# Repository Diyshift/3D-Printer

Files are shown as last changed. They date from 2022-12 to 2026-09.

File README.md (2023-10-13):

# 3D Printing Stuff
A collection of 3D printer tools, mods, and random printables. 

My projects are 100% fueled by coffee. If you enjoy the work I do and would like to buy me one, you can do so here. Thank you for your support! 



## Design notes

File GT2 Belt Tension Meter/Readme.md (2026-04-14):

# GT2 Belt Tension Meter (RC2)

  
  

### DETAILS:
This 3D printed tension meter is designed to measure belt deflection to determine belt tension for Gates 6 and 9mm GT2 belts. The goal is to eliminate the need for phone apps that use frequency to determine tension and to provide an easily quantifiable and repeatable number to use when tensioning belts on a 3D printer. The repeatability and accuracy of this meter will be partially dependent on the build quality but you can expect  approximately ± 1.0N (0.25lb) accuracy on a carefully built and calibrated meter. 

Tested on the following printers: Voron Trident, 2.4, V.0, Salad Fork, and Switchwire.  Note: for other non listed printers please ensure you have clear access to at least 150mm of belt. This meter will not work on printers with belts that run inside of the extrusion channels. 

**CAUTION:** The instructions and tension lookup tables contained herein are to be used with the the RC2 STL files included in this repository only. Any modifications, remixes, or substitutions of the core components have the potential to change the meter's characteristics and accuracy. Many iterations and months of testing were done with the current design (RC2) prior to its release to ensure an accurate and repeatable device. 

---------------------------------------------------------------------------------------------------
**Complete Assembled and Calibrated Meters Available Here:** [](https://www.etsy.com/listing/1508462271/belt-tension-meter-for-3d-printers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) **US** &nbsp;&nbsp;&nbsp;&nbsp; [](https://west3d.com/collections/vendors?q=PF%20Makes) **US** &nbsp;&nbsp;&nbsp;&nbsp; [](https://store.dremc.com.au/products/3d-printer-belt-tension-meter-by-pf-makes?variant=44804998955177) **AU**

---------------------------------------------------------------------------------------------------

### Ready to build your own? 

Below are instructions as well as everything you need to source hardware and get started. For video instructions please check out the excellent step-by-step build guide that LeeMerie3D put together on his Youtube channel here:

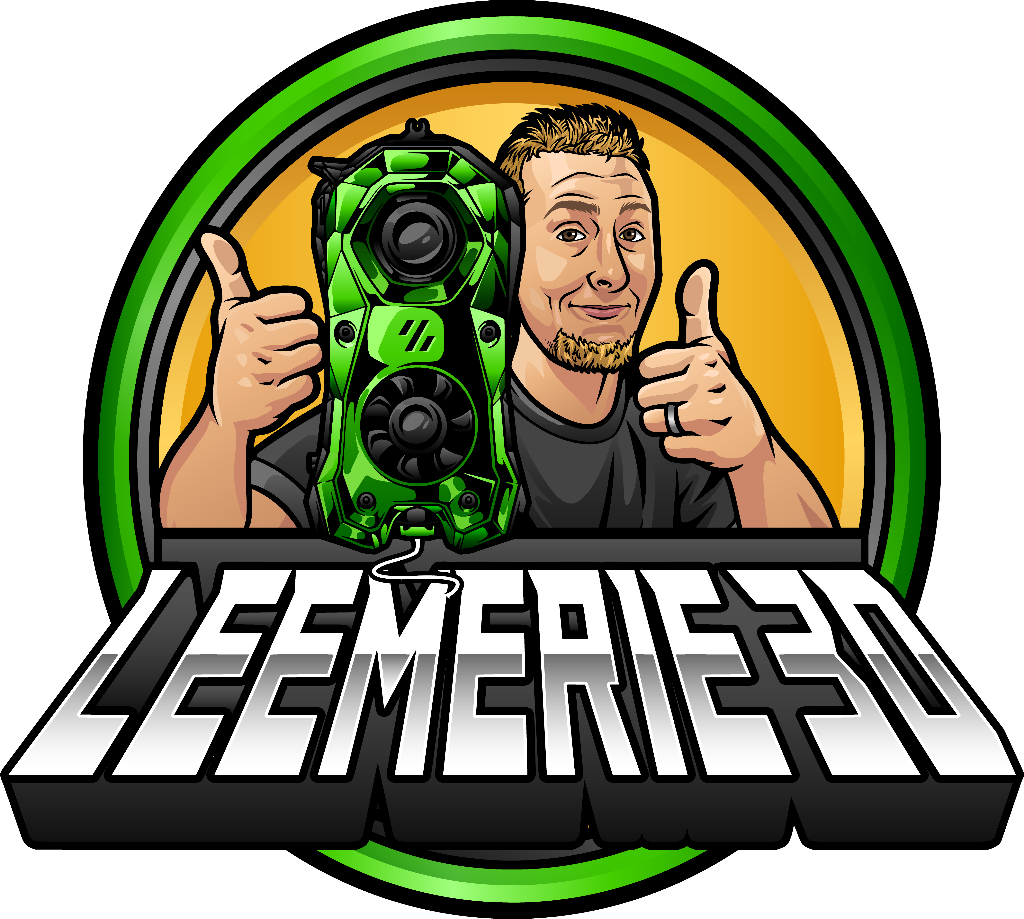
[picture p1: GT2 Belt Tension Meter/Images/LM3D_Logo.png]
[](https://www.youtube.com/watch?v=Ax2ZACkU6S8&t=1s)

### BOM:
Item | Qty
--- | ---
M3x7 Button Head Cap Screw (M3x6 BHCS also works) | 1
M3x25 Socket Head Cap Screw | 1
M3x8x0.6 Washer | 1
M2x10 Socket Head  Self Tapping Screws | 2
[0.81mm x 100mm (0.032” x 4”) Tempered steel music wire AKA "piano wire"](https://ksmetals.com/products/mw-032) | 1
[6mm OD x 0.6mm wire dia. x 50mm free length compression spring with 20 active coils (0.35N/mm spring rate)](https://www.amazon.com/dp/B076LTYY5K?psc=1&ref=ppx_yo2ov_dt_b_product_details) | 1
Complete Set of Printed [Parts](https://github.com/Diyshift/3D-Printer/tree/main/GT2%20Belt%20Tension%20Meter/STLs) | 1

**Complete Hardware Kits Available From The Following:** 

-----------------------------------------------------------------------------------------------------
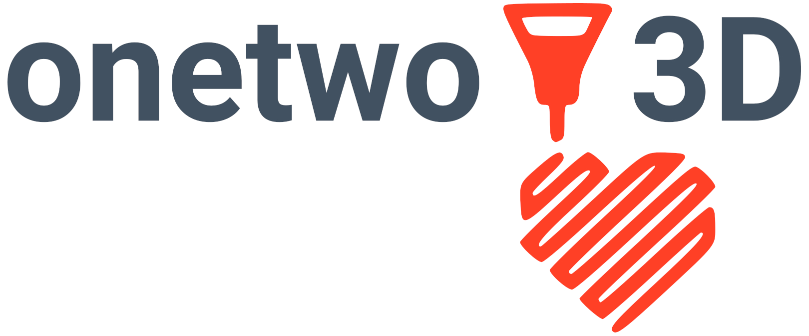
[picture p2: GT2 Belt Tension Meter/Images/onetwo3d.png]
[](https://www.etsy.com/listing/1508474957/hardware-kit-for-diy-3d-printer-belt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) **US** &nbsp;&nbsp;&nbsp;&nbsp; [](https://west3d.com/products/hardware-kit-for-diy-3d-printer-belt-tension-meter-by-pf-makes) **US** &nbsp;&nbsp;&nbsp;&nbsp; [](https://www.viperworx.uk/product/hardware-kit-belt-tension-meter-by-pf-makes) **UK** &nbsp;&nbsp;&nbsp;&nbsp;[](https://www.onetwo3d.co.uk/product/gt2-belt-tension-meter-hardware-kit) **UK**&nbsp;&nbsp;&nbsp;&nbsp;  [](https://store.dremc.com.au/products/3d-printer-belt-tension-meter-by-pf-makes?_pos=1&_sid=28fbfb08b&_ss=r) **AU** &nbsp;&nbsp;&nbsp;&nbsp; 

-----------------------------------------------------------------------------------------------------
[](https://www.3dptronics.com/voron-mods/gt2-belt-tension-meter-hardware-kit-by-pf-makes) **IT** &nbsp;&nbsp;&nbsp;&nbsp; [](https://www.replimat.eu/gt2-belt-tension-meter-hardware-kit/rt10204.2) **DE** &nbsp;&nbsp;&nbsp;&nbsp; [](https://www.3dlabtech.ca/product/belt-tension-meter/) **CA**

-----------------------------------------------------------------------------------------------------

### TOOLS:
 * M3 drill bit and holder 
 * ABS safe grease such as SuperLube Synthetic or Oatey/Harvey's silicone grease
 * 1.5, 2, and 2.5mm hex bit drivers. Ball end hex keys will likely give you a hard time here.
 * Toothpicks and Q-tips for applying grease
 * Hobby knife (X-Acto) 
 * Small flat needle file (optional)
 * Small triangular smooth cut file (for cleaning up gear teeth and tuning dovetail)
 * Cutter capable of cutting hardened music wire (do NOT use your nice flush cutters for this)

### PRINT SETTINGS:
 * Print in ABS or ASA for best results
 * Slide, needle and spring spacer components work best when printed on smooth or satin PEI
 * Layer height 0.2mm
 * 4 perimeters 5 top and 5 bottom layers
 * 40% grid infill
 * Single perimeter tops will improve the dialface text considerably
 * 0.4mm nozzle with 0.4mm line width throughout 
 * No seams allowed on needle or slide gear teeth, use blockers or adjust seam settings in your slicer. 
 * Color change at layer 18 for Base and layer 43 Pivot for dual color contrasting text.
 * Your printer should be well tuned for this project (for example, able to produce a near-perfect Voron cube). Any PA issues or over/under extrusion will likely result in a poorly performing meter.
   
### ASSEMBLY:

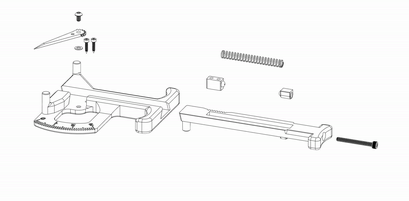
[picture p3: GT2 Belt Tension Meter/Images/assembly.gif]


1. Clean up printed parts as needed. Correct any zits, blobs or other print defects using a small file or hobby knife. Pay special attention to the gear teeth on the slide and needle. Carefully remove any stringing or blobs taking care not to change the tooth profile.
2. Check the fit between the slide and base. It should be loose enough to drop into the base freely without using force. The slide is designed to "float" in the base when in use. See gif below for proper fit. 
   
   

   If your slide it too tight you can adjust the fit in the base by shaving the dovetail in tiny increments with a triangular file on the angled face opposite the dial. 
4. Using a cotton swab, apply a light layer of grease to the spring channel  in the shaded area shown below. Do not lubricate the meter Base or Slide dovetail area as stiction may occur causing inaccurate readings.
5. Insert the spring, spacer, and spring as shown below.

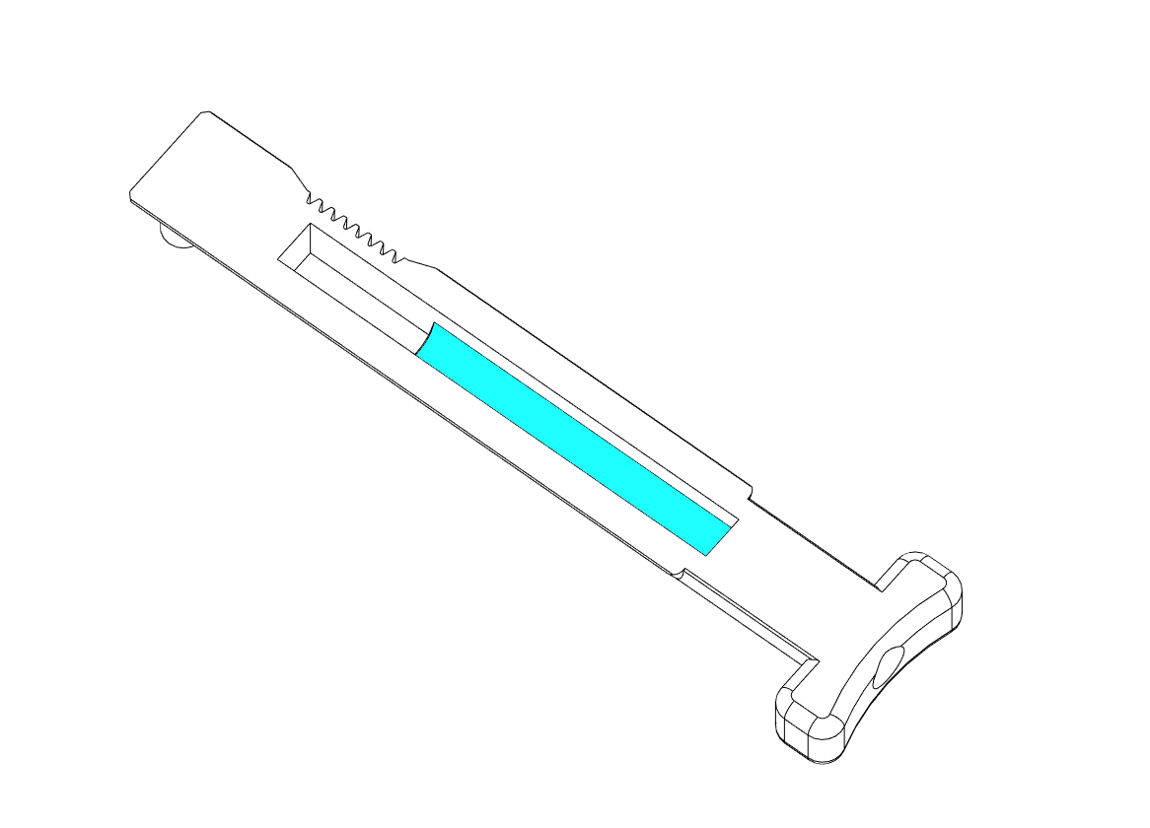
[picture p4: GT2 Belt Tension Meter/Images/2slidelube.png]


5. Insert the spring spacer, spring and spring block in that order as shown. Note of the position of the counterbores on the spring block, they should be facing down in this step.

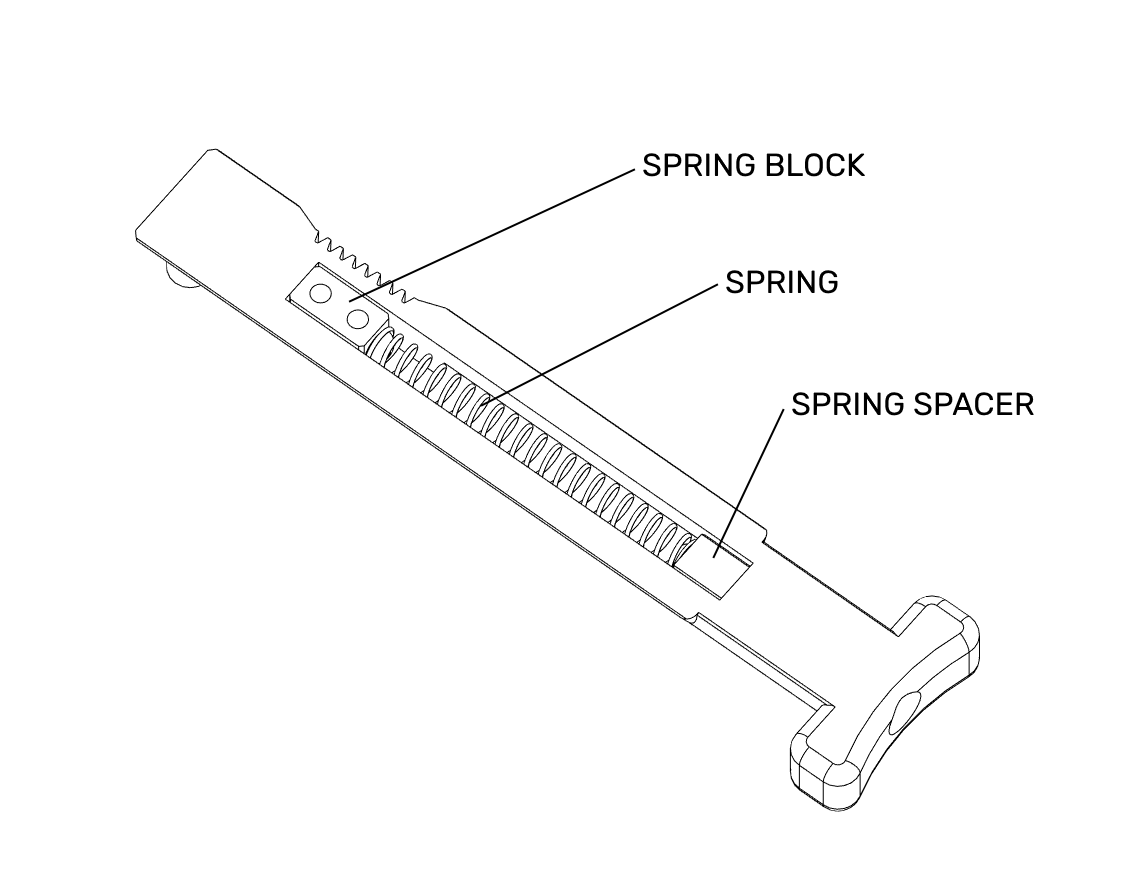
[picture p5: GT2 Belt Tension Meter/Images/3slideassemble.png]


 6. Flip the assembled slide and carefully insert the slide into the base as shown below. Spring tension should hold the parts in place.

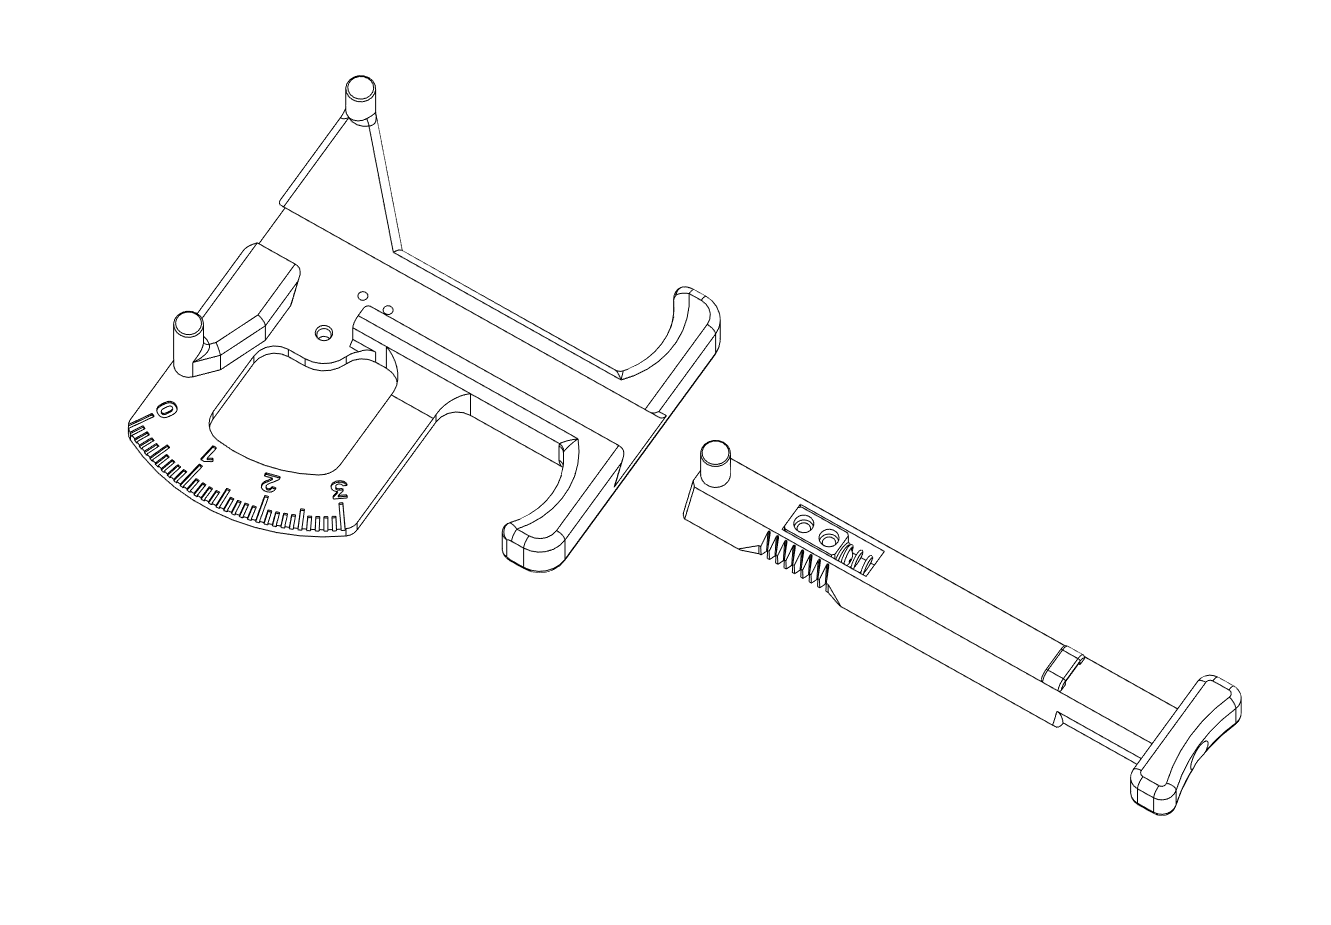
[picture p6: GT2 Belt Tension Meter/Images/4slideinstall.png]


 7. Align the slide with the front of the base so that they are flush and the two holes in the spring block are aligned with the corresponding holes in the base and secure the spring block to the base using two self-tapping M2 screws.

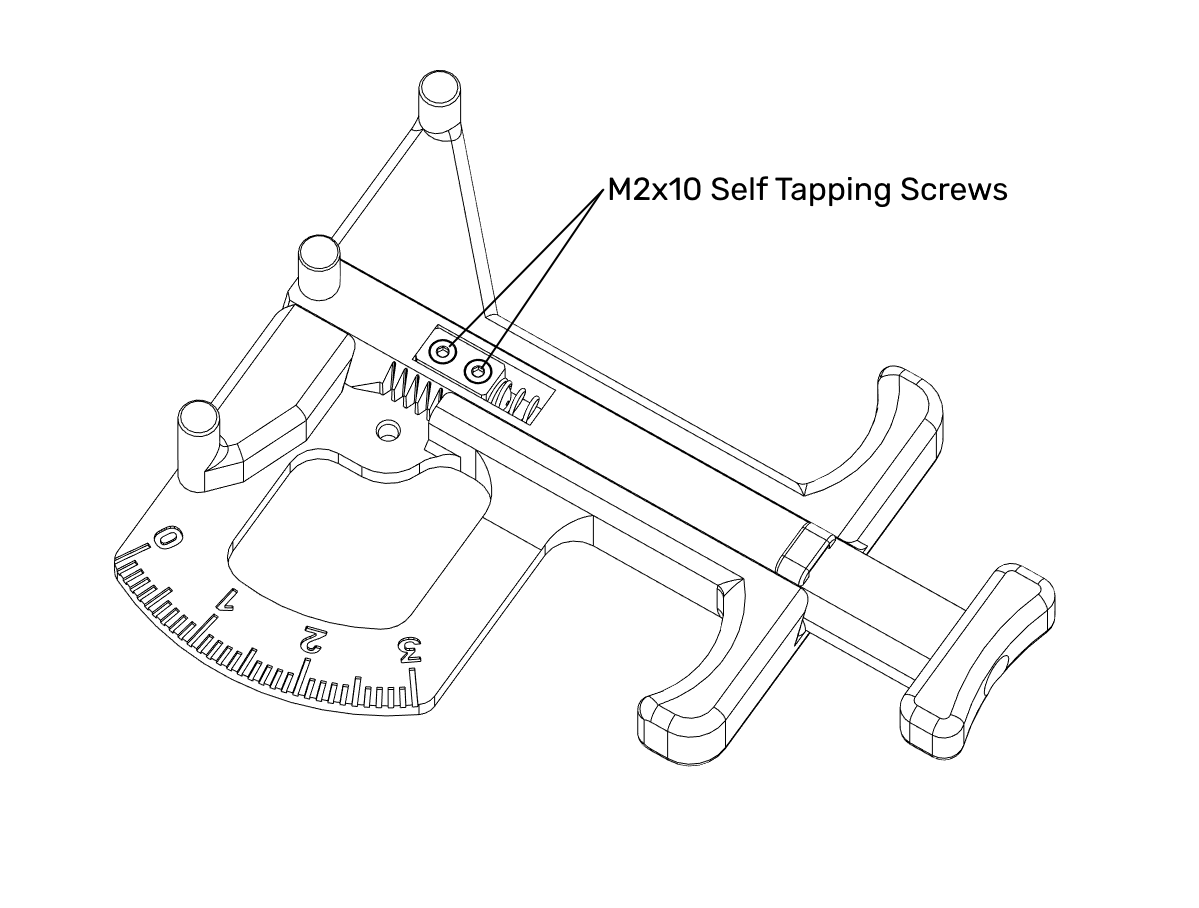
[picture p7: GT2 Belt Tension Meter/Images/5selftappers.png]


8. Depress slide plunger to check that the slide is moving smoothly and without binding.
9. Starting with a #2 needle use trial and error to determine the needle with the best fit. When aligned on the hole, the needle’s teeth will mesh with the slide’s teeth.

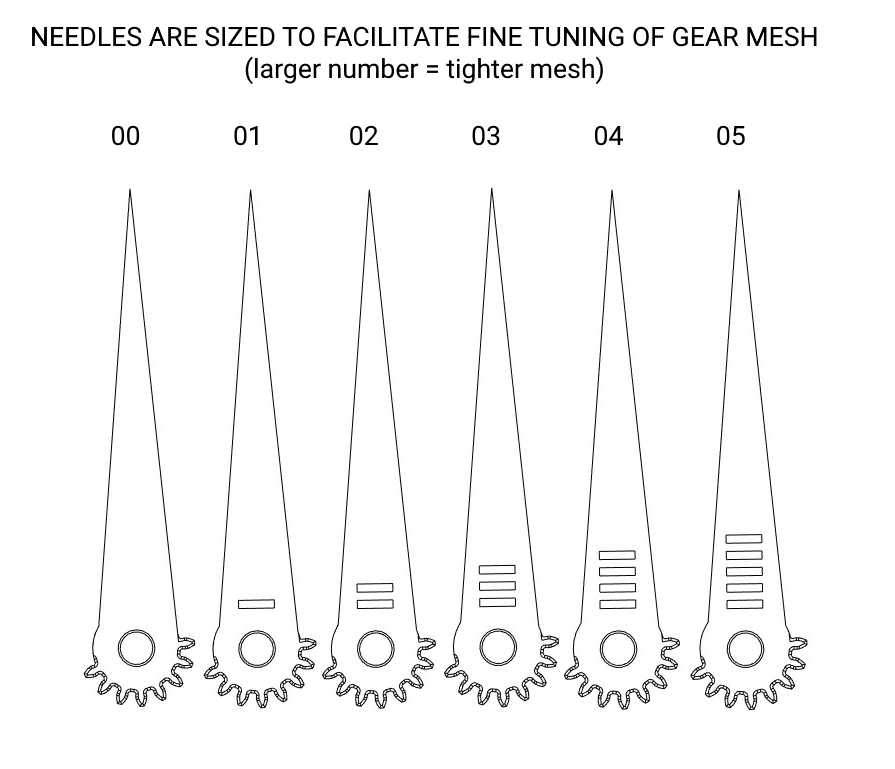
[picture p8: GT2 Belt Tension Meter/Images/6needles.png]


10. Ream the hole in the needle with a 3mm drill bit and check the fit using the M3x25 SHCS screw. The needle should rotate freely under its own weight. (tip: if you don’t own a 3mm drill bit you can use the M3x25 screw to ream the hole by screwing it into the needle and intentionally stripping the threads)
11. Insert the M3x6 BHCS through the top of the needle (as denoted by the circular stamp).
12. Place the M3x8 washer onto the base, aligning it with the hole with the smoothest side up. (some washers have a burr from stamping, this should face down for best result)
13. Secure the needle onto the washer with the M3x7 BHCS, making sure the needle aligns to the zero position and the round divot is facing up. 

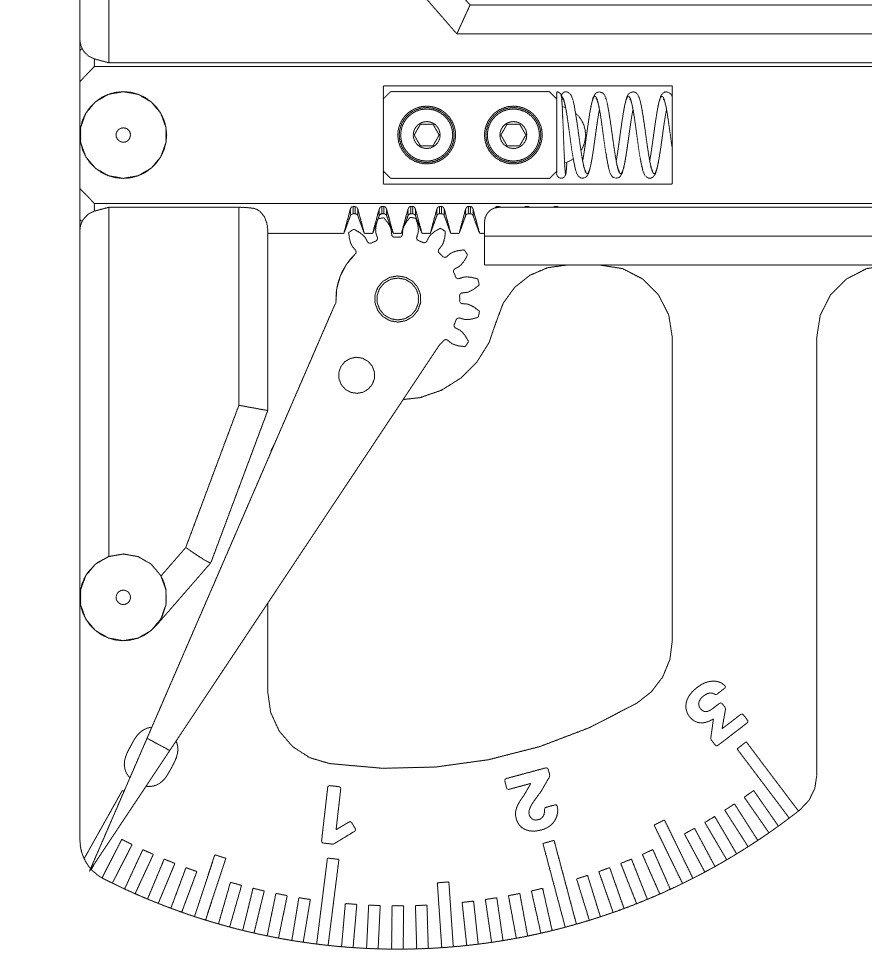
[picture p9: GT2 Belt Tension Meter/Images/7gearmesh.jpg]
 

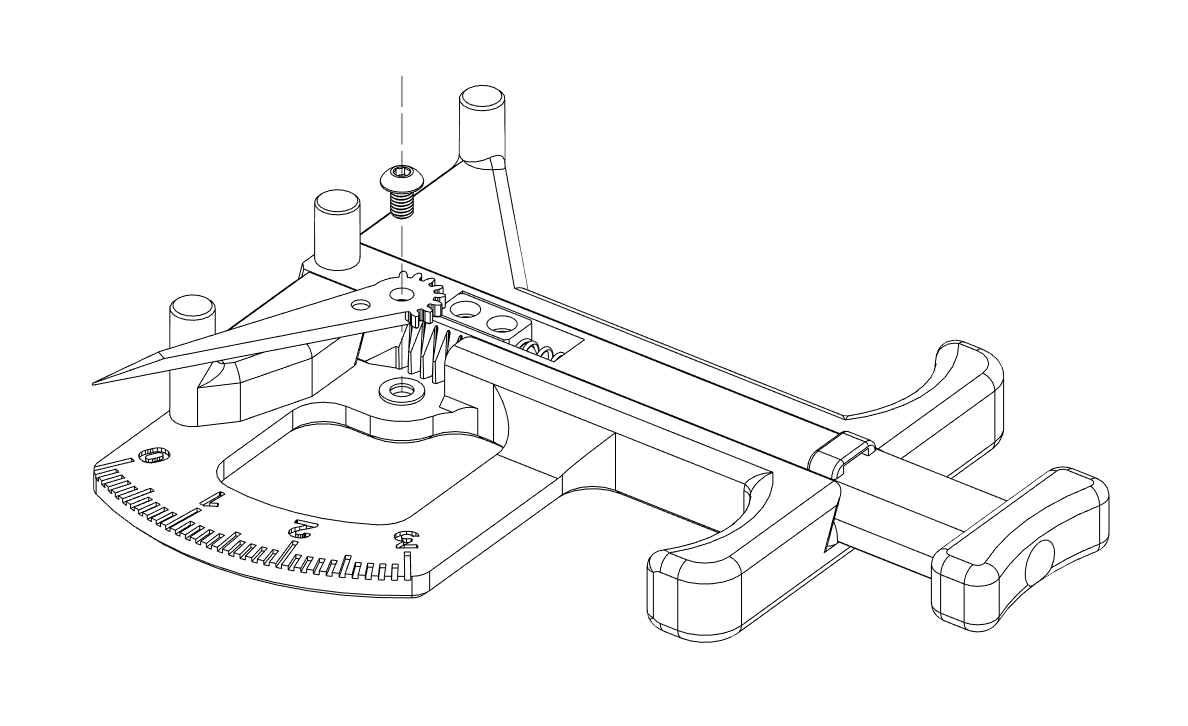
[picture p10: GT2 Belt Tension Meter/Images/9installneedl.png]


14. Tighten screw until just snug then back off in small increments until the needle moves freely.
15. Depress the slide’s plunger several times to ensure that the needle moves freely without jumping or binding.
16. Check the needle’s backlash by gently wiggling with a finger. If the needle moves more than ½ a tick on the dial, swap to the next size up and repeat this test. You want a needle size that gives you the least amount of backlash while still allowing smooth motion of the slide.
17. Once you have the correct needle selected, use a toothpick or similar to apply a very small amount of grease to the areas shown below.
18. Test to confirm that the needle spins freely on the screw.

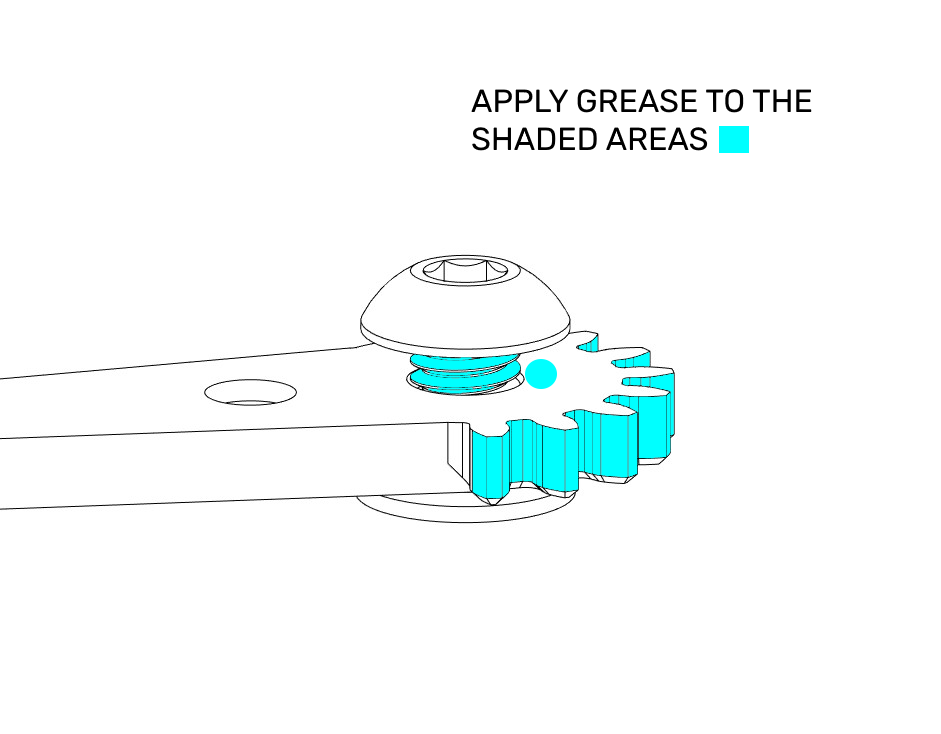
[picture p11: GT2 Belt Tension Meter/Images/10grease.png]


19. Flip the needle over and apply a very light layer of grease to the area that contacts the M3x8 washer, being careful not to get any on the lower threads.

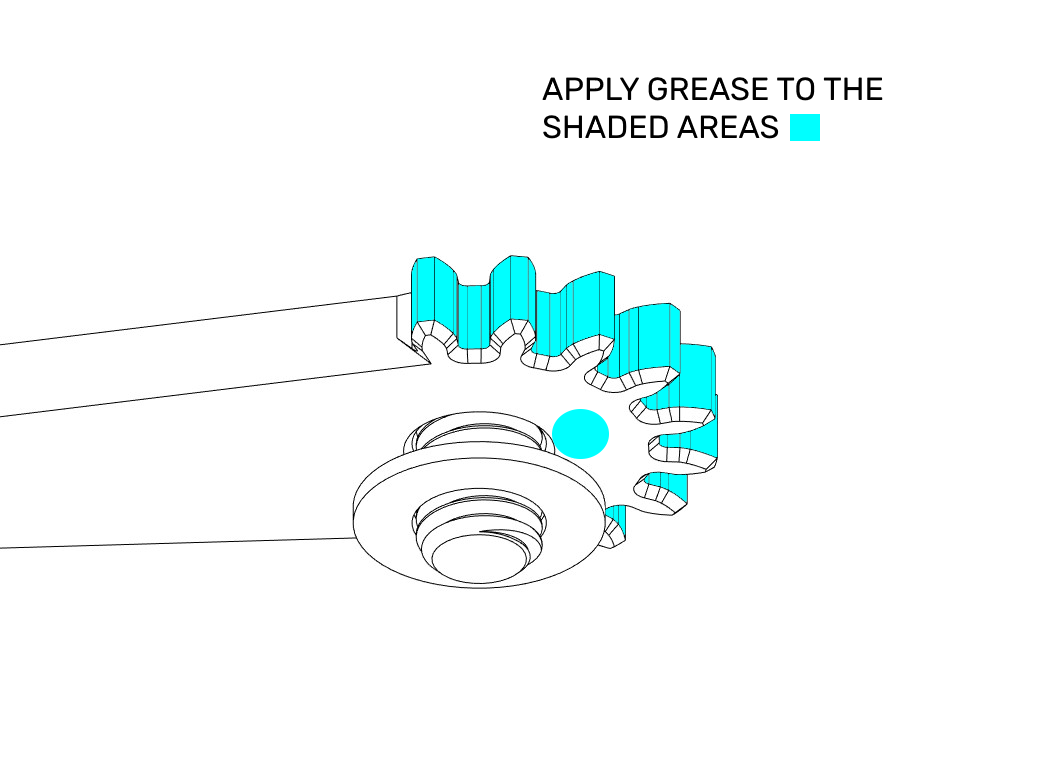
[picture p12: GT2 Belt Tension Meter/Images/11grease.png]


20. Apply a small amount of grease to the teeth on the needle as shown.
21. Place the M3x8 washer back onto the base.
22. Again, tighten the screw until just snug then back off until the needle swings freely.
23. Cycle the slide 20-30 times to make sure grease is distributed and the gears mesh.
24. Slowly cycle the slide several times and observe the needle’s motion. It should be smooth throughout its entire range with no sticking or jumping.  Adjust screw securing needle as needed to facilitate free movement.
25. Finally, install the M3x25 SHCS Preload Screw into the slide plunger as shown. This screw is threaded into plastic. Tighten until the head is flush with the plunger. Your meter is now assembled and ready for calibration.

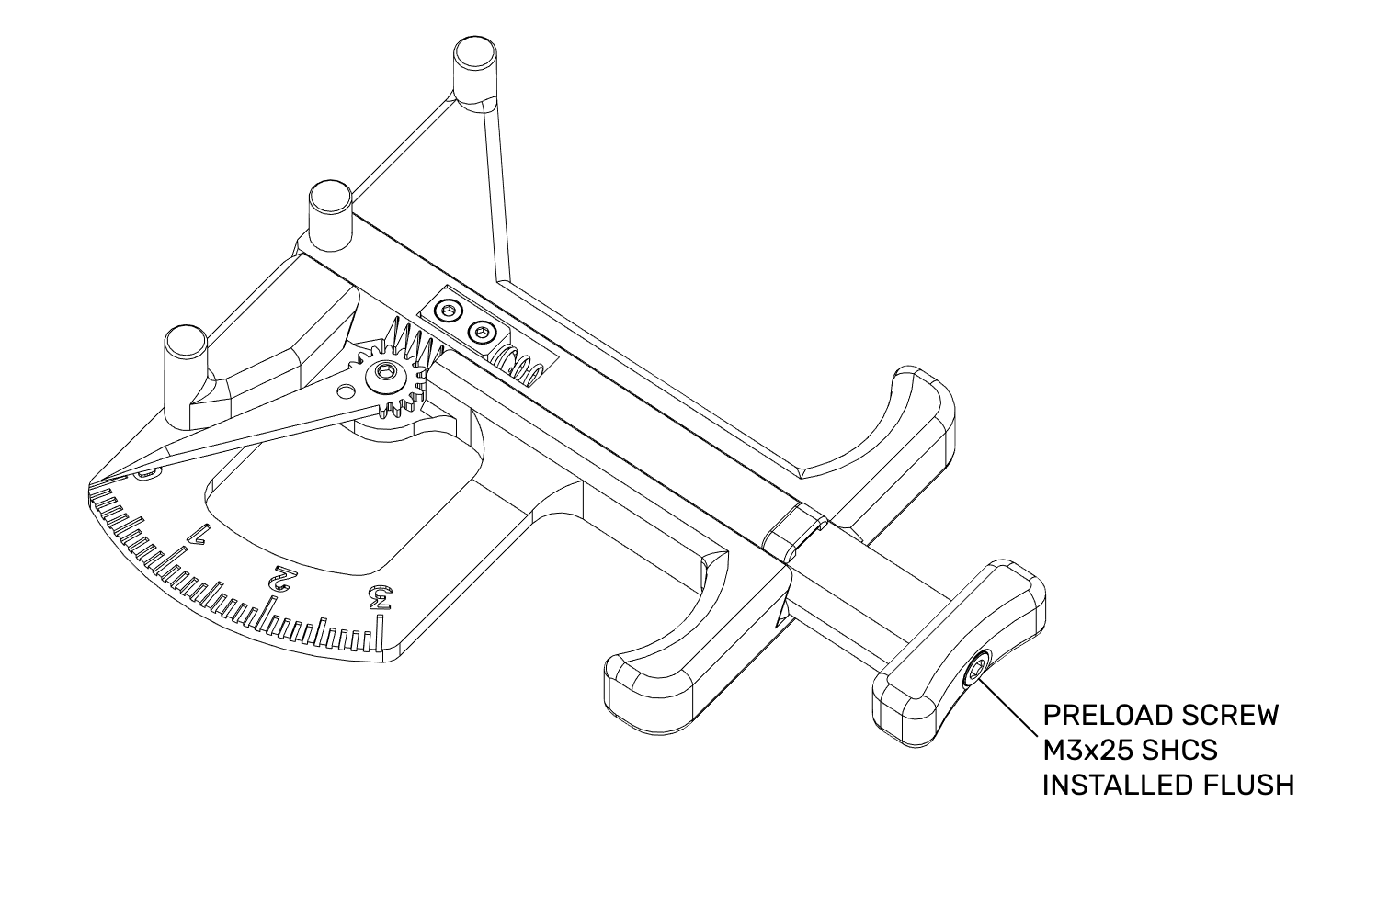
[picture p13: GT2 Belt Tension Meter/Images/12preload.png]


**Note:** If your meter dial is not resting on the zero mark you may need to loosen the two self tapping screws slightly in the spring block move needle to zero position then tighten screws back down. 

### CALIBRATION:

1. Cut music wire to 100mm and deburr the ends with a file.  (note: do not use your good side cutters for music wire, dremel cutoff or hard wire cutter recommended).
2. Glue the wire into the hole on the side of the calibration handle making sure it is fully seated and flush on the opposite side. Afterwards remove any burrs or glue from the hole in the calibration pivot. It should rotate freely on the left pin when installed.

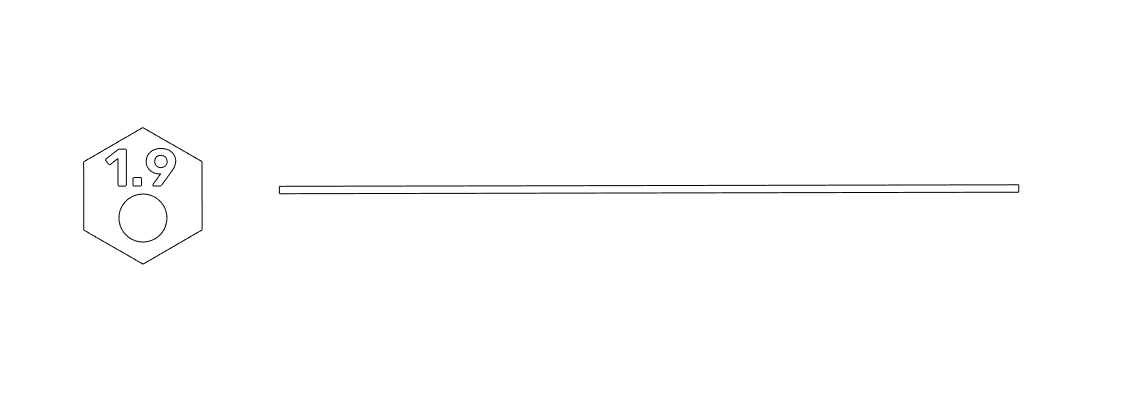
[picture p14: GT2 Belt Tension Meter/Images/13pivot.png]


3. Depress plunger and place calibration wire into the jaws making sure the pivot is seated all the way on the left pin as shown. Eye protection is recommended for this step.

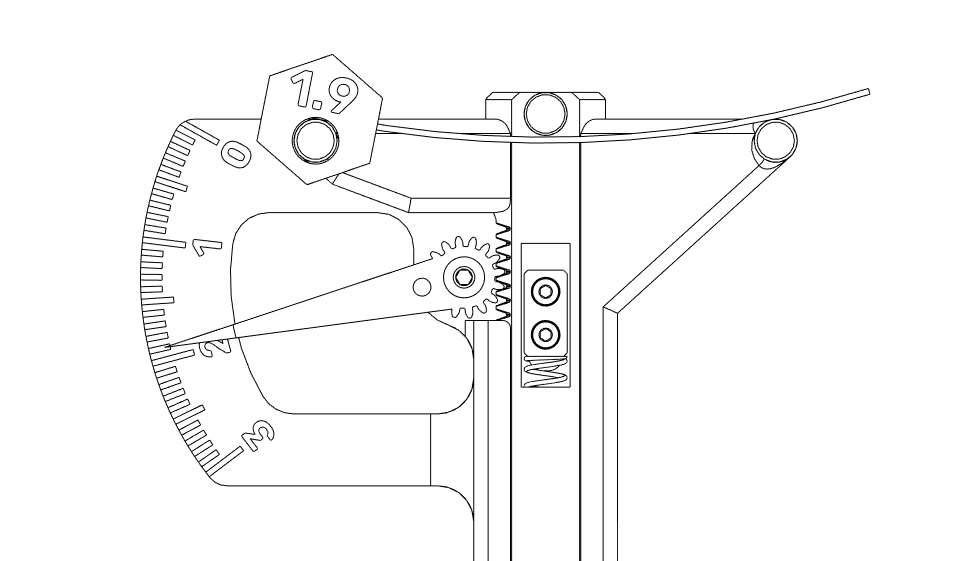
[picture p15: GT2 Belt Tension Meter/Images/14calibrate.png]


4. Slowly release the plunger and note the reading on the dial. Lightly tapping or “pumping” the plunger handle can help to settle the needle and get a better reading.
5. Tighten the preload screw one turn then depress and release the plunger again. Note that the reading has changed.
6. Repeat steps 3 - 5 until your meter consistently reads 1.9 when checking the deflection of the music wire.
7. Your meter is now calibrated and ready for use.

 ### ALTERNATIVE CALIBRATION:  
If straight tempered music wire is not available a suitable weight and spare section of belt can be used. A gallon plastic water jug and scale works well for this. Do not trust weights marked on fitness equipment, weigh them first. 

1. Suspend a 1.36Kg (3lb) weight vertically from a 250mm section of GT2 belt and measure the tension with the belt teeth in contact with the two outer pins on the meter as shown below in step 3.
2. Adjust the preload screw as needed until the meter reads consistently across several measurements.  2.1 for standard rubber or 2.2 EPDM high temperature belt.

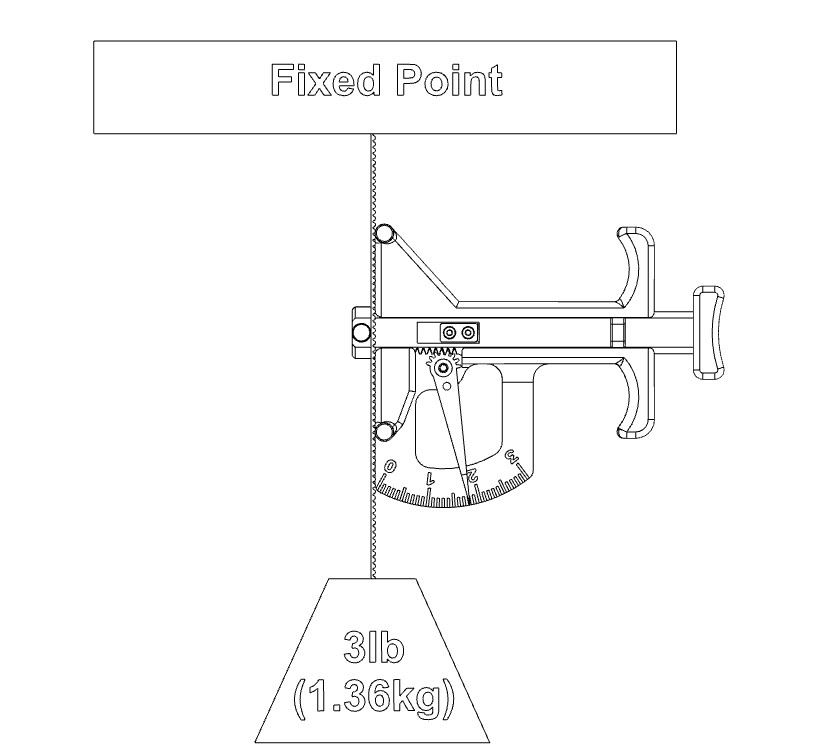
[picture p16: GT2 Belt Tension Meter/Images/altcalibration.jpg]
   

Calibration wire can be stowed on the center pin with wire secured beneath the slides wire keeper. 

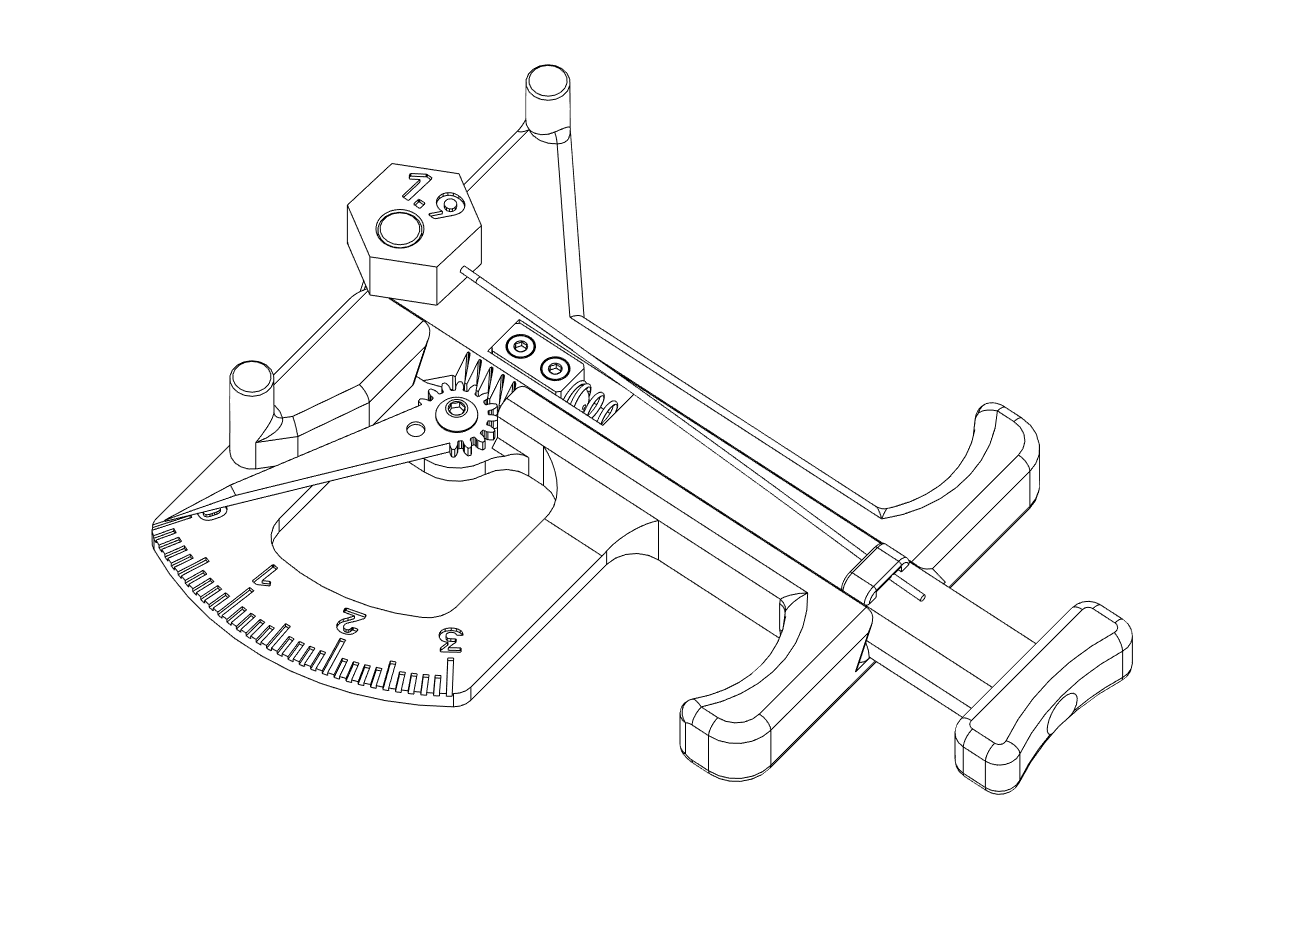
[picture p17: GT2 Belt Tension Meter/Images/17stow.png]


 ### TENSION MEASUREMENT A/B BELTS: 

 1. Printer should be cold for this test.
 2. Refer to your printer's documentation for proper belt tension or see table below.
 3. Center toolhead on X and then move Y until the X/Y idler centers are 150mm from the front idler centers. Motors should be on for this test. (note: unlike phone apps the 150mm distance is not a critical distance just a way to ensure that the toolhead is centered and to aid in obtaining repeatable results).
 4. Depress plunger and place meter on the 150mm belt span so that belt is routed through the gauge pins as shown.

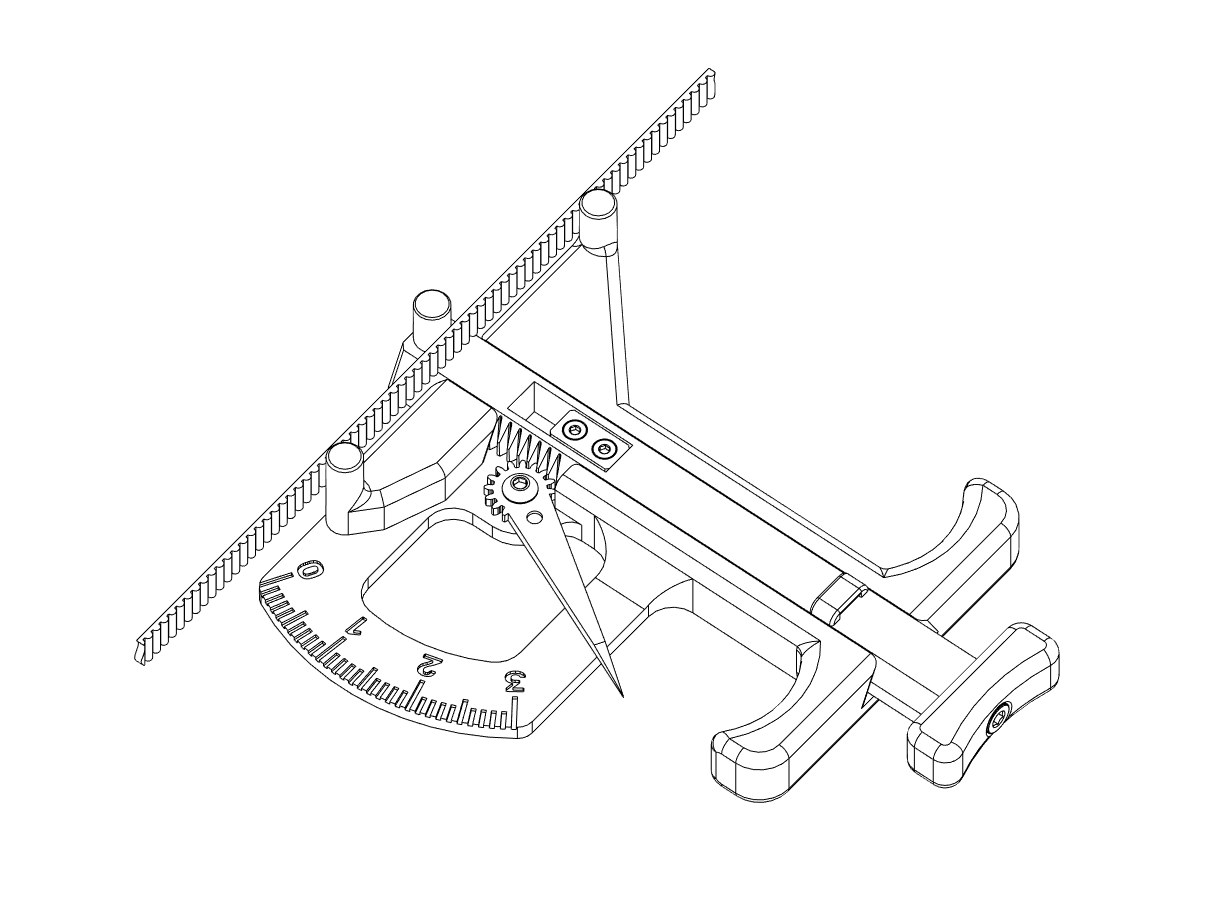
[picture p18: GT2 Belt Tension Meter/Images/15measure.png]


 5. Slowly release the plunger and note the reading on the dial. *rocking the meter very slightly fore and aft or lightly “pumping” plunger can help to settle the needle and get an accurate reading.
 6. Repeat three times to ensure you are getting consistent readings.
 7. Adjust belt tension then repeat steps 3-5 until you reach the desired tension (see table below) The A/B belt tensions can affect each other. Tightening one will also tighten the other. Go back and forth adjusting each until they are equal.

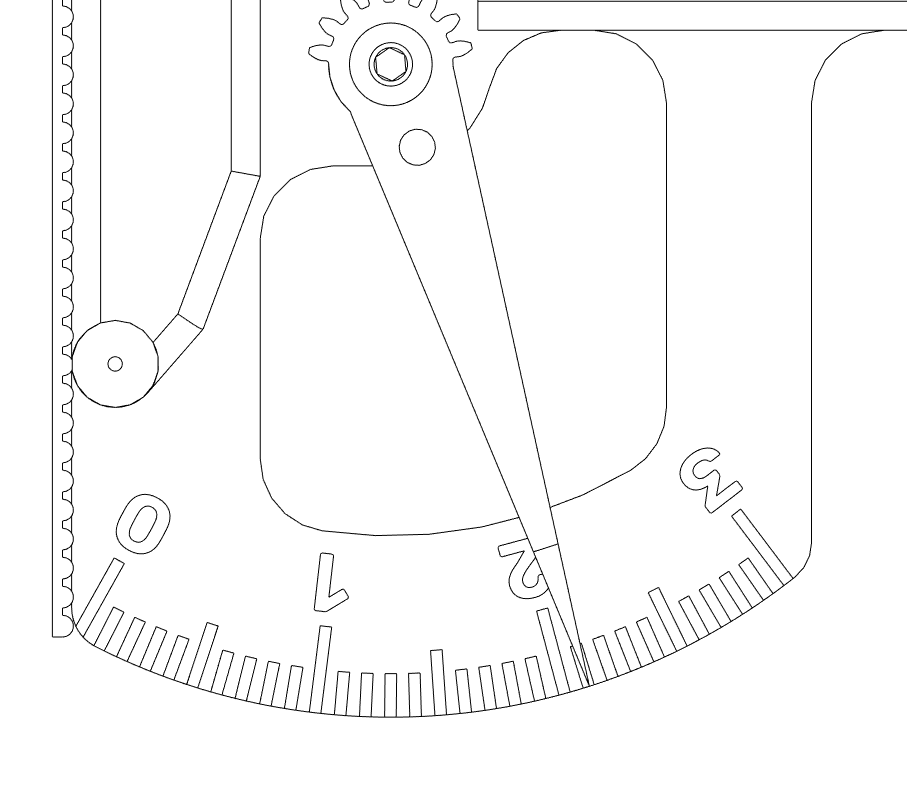
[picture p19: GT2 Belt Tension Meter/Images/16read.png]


8. Home X and Y to seat the belts then repeat steps 2-5 to verify that tension is correct and make followup adjustments as needed.
9. Your belts should now be properly tensioned. 

Note:  Depending on your style of printer your belt tension may increase slightly when utilizing a heated chamber so keep this in mind when selecting tensions in the higher range. Check your belts after a preheat to be sure you are not exceeding safe limits. When checking tension always remember to run the measured axis through its full range of travel before measuring to normalize the tension in the belt path. 

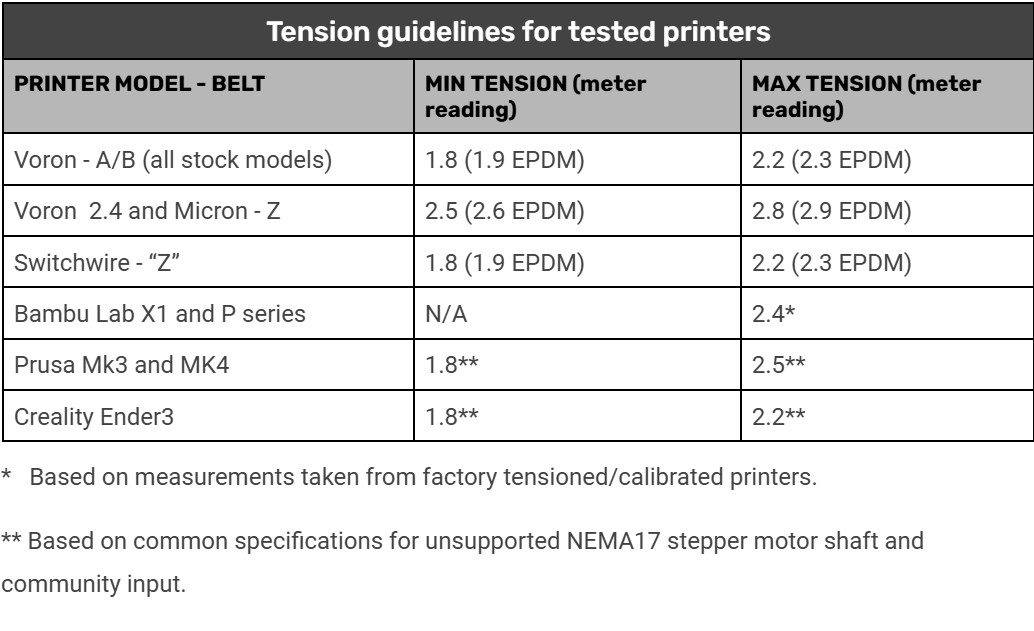
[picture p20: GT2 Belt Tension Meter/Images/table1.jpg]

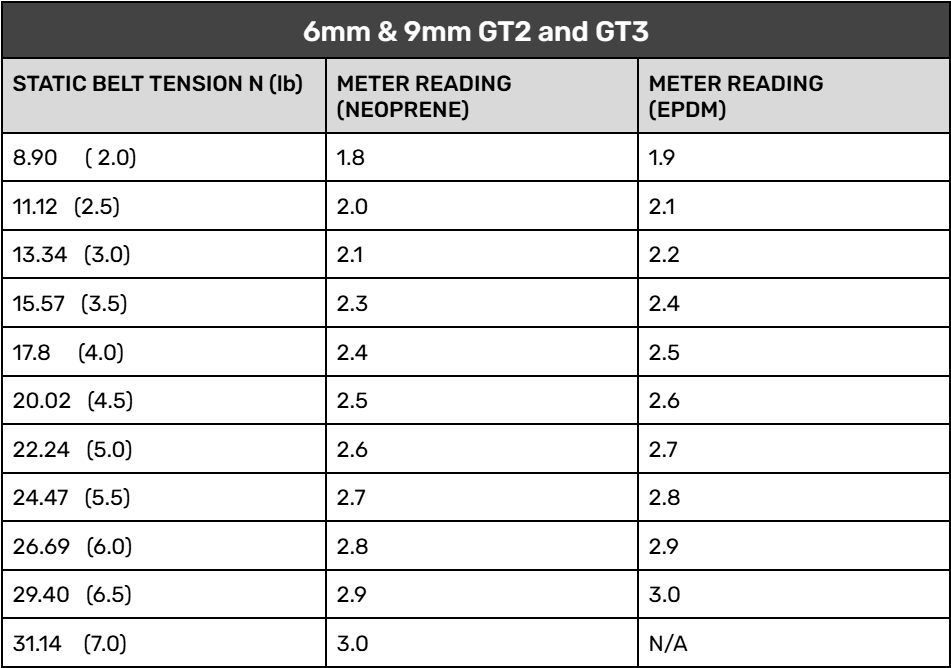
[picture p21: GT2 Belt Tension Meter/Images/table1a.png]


### Need a handy tension chart sticker?  Dr. Mursey has them here in his sticker shop: 

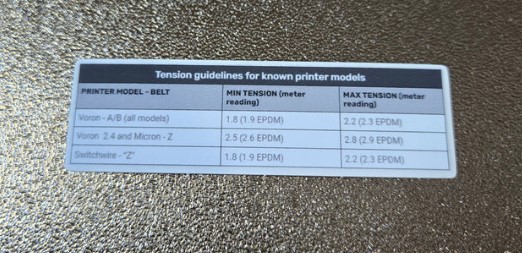
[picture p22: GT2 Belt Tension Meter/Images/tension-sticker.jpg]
[](https://drmursey.myshopify.com/products/pf-tensioner-chart)

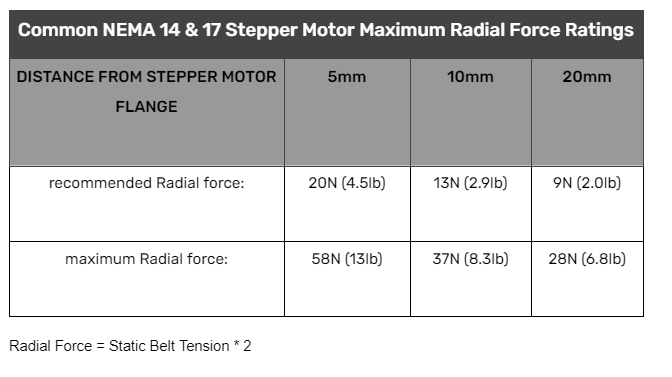
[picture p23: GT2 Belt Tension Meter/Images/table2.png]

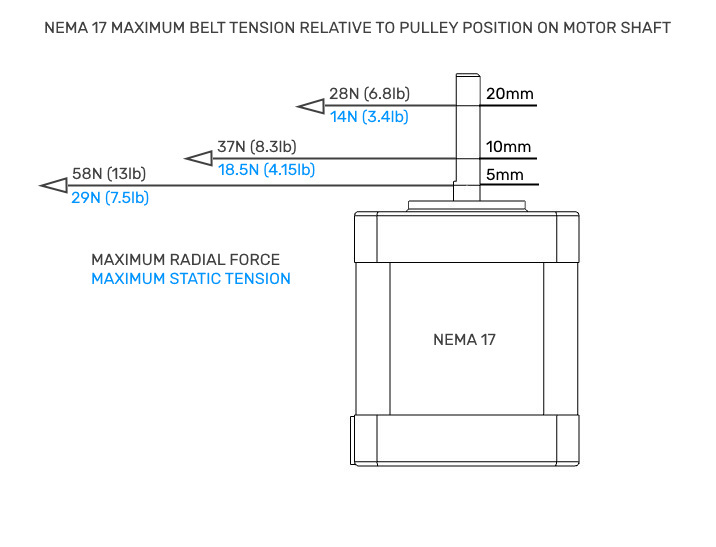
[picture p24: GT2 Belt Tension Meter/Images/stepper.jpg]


### CREDITS
Sincere thanks to the following for donating their time, plastic, and patience in helping to test and provide feedback on this design: 
 * Le0n2959
 * Moogoo (oogoom)
 * Yeri (yeriwyn)
 * Dokuu
 * Xivima
 * Mc-Red
 * Lillianamirrors
 * Pnewb



 My projects are 100% fueled by coffee. If you enjoy the work I do and would like to buy me one, you can do so here. Thank you for your support! 



This work is licensed under a
[Creative Commons Attribution-NonCommercial-ShareAlike 4.0 International License][cc-by-nc-sa].

[][cc-by-nc-sa]

[cc-by-nc-sa]: http://creativecommons.org/licenses/by-nc-sa/4.0/
[cc-by-nc-sa-image]: https://licensebuttons.net/l/by-nc-sa/4.0/88x31.png
[cc-by-nc-sa-shield]: https://img.shields.io/badge/License-CC%20BY--NC--SA%204.0-lightgrey.svg

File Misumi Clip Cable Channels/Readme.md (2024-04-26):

# Misumi Clip Cable Channels
 ### A collection of clips for 2020 extrusion to form channels to run/hide your wires 
 Now available for 1515 extrusions! See 1515 folder under STLs 
 


### Printing
  * Default voron settings
  * No supports needed

### Instructions:
 
Snap into extrusionslots to form wire channels. Cutouts models are provided for wire entry/exit. Shown here on vertical extrusions using the main channel clip for Trident:




Wire cutouts can also be used at at the top motor exits.  Thank you Voron Discord user cousin it VS.570 VT.1233 for this idea and image!


These are a modified version of Eddie's fantastic LED clips that can be found here: https://github.com/VoronDesign/VoronUsers/tree/master/printer_mods/eddie/LED_Bar_Clip

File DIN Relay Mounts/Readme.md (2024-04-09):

# DIN Relay Mounts 
 ### Mount single or dual channel relays on electonics bay DIN rails




### BOM

Size | Qty
--- | ---
Single or Double Channel Relay       | 1
Voron pcb_din_clip                       | 1
M2x6 Socket Head Self-Tapping Screws | 6

Relay screw hole spacing:  

Single Channel:  20mm x 45mm

Dual Channel:    33.25mm x 45mm

DIN Clip: https://github.com/VoronDesign/Voron-2/blob/Voron2.4/STLs/Electronics_Bay/pcb_din_clip_x3.stl

Dual Channel Relay: https://www.amazon.com/gp/product/B078478SZ9/ref=ppx_yo_dt_b_search_asin_title?ie=UTF8&psc=1

Single Channel Relay: https://www.amazon.com/gp/product/B00LW15A4W/ref=ppx_yo_dt_b_search_asin_title?ie=UTF8&psc=1

### Printing
  * Default voron settings
  * No supports needed

### Instructions:

  * Mount pcb_din_clip to the relay mount base using 2 M2x6 Socket Head Self-Tapping Screws
  * Install relay to mount using 4 M2x6 Socket Head Self-Tapping Screws

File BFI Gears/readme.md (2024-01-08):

# Trident Beefy Front Idler Gears (alpha version)
 ### Gears to keep your top and bottom tension adjustment screws in sync. For Clee's fantastic beefy front idlers found here: https://github.com/clee/VoronBFI



### BOM

Size | Qty
--- | ---
M3x8 BHCS    | 1
M3x6 BHCS (for recessed idler gear only) | 1

### Printing
  * Default voron settings
  * No supports needed

### Instructions:

  * Glue two larger gears to the heads of your M5x40 SHCS using superglue
  * Install BFI as you normally would and adjust top and bottom M5x40 SHCS so that belt runs centered 
  * Once centered install the smaller idler gear using an M3x8 BHCS screw (or M3X6 BHCS for recessed idler) do not overtighten. 
  * Gears should be a snug fit to eliminate backlash. Scale the center idler gear if needed to acheive a good fit.
  * If you would like or need more clearance print and install the recessed idler gear and use an M3x6 BHCS instead.

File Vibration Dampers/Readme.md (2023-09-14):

# Vibration Damping Coasters
 ### Uses sorbothane rings to dampen printer vibration 





### BOM

Size | Qty
--- | ---
Isolate It: Sorbothane Vibration Isolation Washer 70 Duro (0.5" ID - 1.5" OD - 0.5" Thick)* | 4
Self adhesive cork or similar anti skid (optional) | 4

*tested with Voron Trident 300, smaller lighter printers will likely require a lower durometer

### Printing
  * Default voron settings
  * No supports needed

### Instructions:
 
Add anti-skid cork or similar to bottom of cup and trim.  Place the sorbothane ring in the cup, then install the cap as shown and install underneath your stock printer feet.   



### My Trident input shaper results before and after adding the dampers: 



### Input shaper results with the ADXL mounted to my desk to measure its vibration: 



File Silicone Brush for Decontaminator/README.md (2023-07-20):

# Silicone Brush Mod for Decontaminator

A silicone brush mod for the Edwardyeeks decontaminator and brush mod that can be found [here](https://github.com/VoronDesign/VoronUsers/tree/master/orphaned_mods/printer_mods)

If you need this brush for your V0.2 check out MurseyThings remix [here](https://www.printables.com/model/522524-v02-nozzle-wiper-silicone-remix)

This design uses an inexpensive silicone bracelet that is cut into 18mm long segments to form the "bristles" of the brush using the supplied cutting guides. The cut silicone pieces are then placed into the slots in the brush holder and secured via a M3x50mm socket head caps screw. Sharpening the tip of the M3x50 SHCS to a point with a file is recommended but not necessary. If you choose not to sharpen the screw you can simply pierce the installed silicone flaps using the hole in the cut guide first with a tack or other shrarp object to make installing the unsharpened screw easier. 



### BOM

Size | Qty
--- | ---
M3x50 | 1
Heat-set Insert | 1
Silicone Wrist Band | 1 (2 if longer bristles are desired)

[CAD for alternative bristle guides](https://github.com/Diyshift/3D-Printer/tree/main/Silicone%20Brush%20for%20Decontaminator/CAD)

### Step 1.  Use the printed cutting guide to form the bristles. Print both guides and alternate 3 and 4 bristles segments in the brush holder.



### Step 2. Use a sharp object to pierce the the segment via the hole in the cutting guide. 



### Step 3. Ensure the band is fully inserted in the guide and make the final cut to length. 



### Step 4. Insert heat set insert followed my alternating 3 and 4 bristle segments. Make sure segments are fully seated and install the M3x50 Screw



### Step 5. Install your new silicone brush, check brush height and adjust as needed. 

The wrist bands I used for this can be found here: https://www.amazon.com/gp/product/B09263TPL9/ref=ppx_yo_dt_b_search_asin_title?ie=UTF8&psc=1  However any silicone band measuring approx 12mm wide and 2mm thick should work. If you have a soldering iron it is a good idea to test your bands first to ensure that they are in fact silicone and heat resistant enough to use for cleaning a heated nozzle. They should not melt when touched with the tip of the hot iron. 



Rainbow barf brush image courtesy of Discord user brad__r 

Thank you Le0n#2959 for the helping brainstorming the cutting guide! :)

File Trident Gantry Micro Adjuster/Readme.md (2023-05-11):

# A fidgety over complicated way to keep your extrusions in place while adjusting Trident rear gantry extrusion height

### BOM

Size | Qty
--- | ---
M3x10 | 3
M3x20 | 2
M3 Hammer Nuts | 3
M3 Nuts | 2



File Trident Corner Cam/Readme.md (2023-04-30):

# Trident Corner Pi Cam 
 ### 

View on 300 Trident with 150° lens

### BOM

Size | Qty
--- | ---
Arducam Arducam Lens Board OV5647    | 1
150° M12 Wide Angle Lens             | 1
1 Meter FFC Pi cam Cable             | 1
M3x5 BHCS                            | 3
M3x8 SHCS                            | 2
M3 Hammer Nuts                       | 1
M3 Heat Set Insert                   | 1
M2x6 Socket Head Self-Tapping Screws | 4

Pi Cam https://www.amazon.com/gp/product/B013JTY8WY/ref=ppx_yo_dt_b_search_asin_title?

150° Lens https://www.amazon.com/gp/product/B07FXF9Y1V/ref=ppx_yo_dt_b_search_asin_title?

Long FFC cable https://www.amazon.com/gp/product/B088CVNQHL/ref=ppx_yo_dt_b_search_asin_title?ie=UTF8&psc=1

### Printing
  * Default voron settings
  * No supports needed

### Instructions:

  * Mount Top Bracket to extrusions using M3x8 SHCS and hammer nuts. *this version is for left side mount only
  * Install Heatset in yoke then attach to Top Bracket using M3x6 BHCS. 
  * Insert FFC cable into the Pi cam module and secure. 
  * Pass FFC cable through rectangular slot in bottom of Cam Body. 
  * Insert Pi cam board into Cam body then install cover securing it with the M2x8 Socket head self tapping screws. 
  * Secure the completed camera module to the Yoke using 2 M3x6 BHCS threading them into the plastic of the Cam Body. Tighten only enough to hold the camera in      position, do not overtighten. 
  * Snap-in FFC cable channels are included to route your FFC cable down the vertical corner extrusion and into your electronics bay. There should be enough clearance to pass the FFC between the top deck panel and the frame. Use a 90° bend in the FFC cable and conseal with the exit port channels as shown. 
 




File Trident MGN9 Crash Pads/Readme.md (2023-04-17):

# Trident MGN9 Z Crash Pads

 ### Limit Z travel to minimize damage to X gantry and components in the event of a homing crash. Whoa means whoa!




### BOM

Size | Qty
--- | ---
Printed Crash Pad A.stl        | 3
Printed Crash Pad B.stl        | 3
M3x16 Socket Head Cap Screws   | 3
M3x5x4 Heat Set Inserts        | 3

### Printing
  * Default voron settings
  * No supports needed

### Instructions:

  * Install the tickest print bed/surface you plan to use. 
  * Home printer, Z-tilt
  * calibrate_z (only if using auto Z offset)
  * Center toolhead over bed and move to Z0 
  * Wipe any grease off of linear Z rail above the Z carriage and attach the crash pad as shown
  * Place 2-3mm hex key between the crash pad and the Z carriage to set the height
  * Tighten firmly and check to make sure it does not move
  * Now if z homing fails for any reason your z travel will be limited to Z-3. While this won't save your PEI it will stall the motors and prevent twisting your X extrusion and or breaking your X carriage components.

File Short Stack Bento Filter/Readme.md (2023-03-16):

# Short Stack Bento Box Carbon/HEPA Filter
 ### A shortened remixed version of the wonderful original design found here: https://www.printables.com/model/272525-bambu-lab-x1c-bentobox-air-filter



### BOM

Size | Qty
--- | ---
40x10 Axial Fan | 2
M3x8 Socket Head Cap Screws | 10
M3 Heat Set Inserts | 12
M3 Hammer Nuts | 2
40x80x15mm Hepa Filter | 1
6x3mm N52 Disc Magnets | 32
Acid-Free Activated Carbon

### Printing
  * Default voron settings
  * No supports needed

### Instructions:
In addition to shortening the modules, this remix relocates the wiring channels for cleaner wiring when used on Voron printers as well as mounting holes to secure it to the rear 2020 extrusion. For Trident mount the duct to 2020 rear extrusion using the two rearmost through holes, M3x8 screws and hammer nuts. Then secure fan mount and stack the remaining modules. 



This version for use with this size HEPA filter only: https://www.amazon.com/gp/product/B0782T7L6P/ref=ppx_yo_dt_b_search_asin_title?ie=UTF8&psc=1

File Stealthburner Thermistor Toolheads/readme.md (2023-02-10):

# Stealthburner Heatsink Thermistor Mod for Dragon Hotends
 ### Allows you to monitor the temperature of your heatsink where it mounts to the toolhead. Klipper can be configured to shutdown if this gets too hot in the event of a hotend fan failure.   



### BOM
100K Ohm NTC 3950 glass bead thermistor. (bead should measure approximately 1.6mm diameter x 3.3mm in length)

Here are the ones I use in my printersfor this mod. 
https://www.amazon.com/gp/product/B098TF372P/ref=ppx_yo_dt_b_search_asin_title?ie=UTF8&psc=1

### Printing
  * Default voron settings
  * No supports needed
  * Only the included rear portion of Stealthburner toolhead is needed to inplement this mod

### Instructions:
 Add a small dab of thermal grease to the thermistor before assembly. 
 
After connecting the thermistor to your control board add the thermistor entry to your printer.cfg file. I recommend setting at a lower shutdown temp to test before setting your final max_temp value
 
printer.cfg example: 

[temperature_sensor heatsink_temp]

sensor_type: Generic 3950

sensor_pin:      #port that thermistor is plugged into

min_temp: 0

max_temp: 50     #halt printer if ABS deflection temp is exceeded set to 90 after sucessful shutdown test at 50

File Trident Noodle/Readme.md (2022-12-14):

# Trident Reverse Bowden Noodle
Reverse bowden tube guide to keep it from rubbing the top panel.  Inspired by Logan#2225's clip on version.
 


### Printing
  * Default voron settings
  * No supports needed

### Instructions:
 
Slide onto reverse bowden tube prior to inserting into extruder coupling.

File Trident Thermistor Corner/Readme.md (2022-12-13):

# Trident Frame Thermistor Corner
 ### Mr. Thermistorfoot lets lets you cleanly run your thermistor from your electronics bay up through the center of your vertical extrusions for frame temp monitoring and thermal expansion compensation.  



### Printing
  * Default voron settings
  * No supports needed

### Instructions:
 
This is the A corner, so this will place your thermistor in the left-rear or front-right corner.

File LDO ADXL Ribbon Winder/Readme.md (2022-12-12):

# LDO ADXL Ribbon Winder
 ### Stores FFC ribbon cable for LDO Input Shaper Toolkit. 



### Printing
  * Default voron settings
  * No supports needed

### Instructions:
 
Snap halves together then line up the slot with the arrow on the lid. Insert the end of the ribbon cable and push until it stops. Use the large hole in the lid to wind up with your finger until just the blue tab is showing. Grasp knurled case and pull the ribbon when you need to remove it. 

You can view it in action here: https://youtube.com/shorts/ohC4sa6RvPU?feature=share



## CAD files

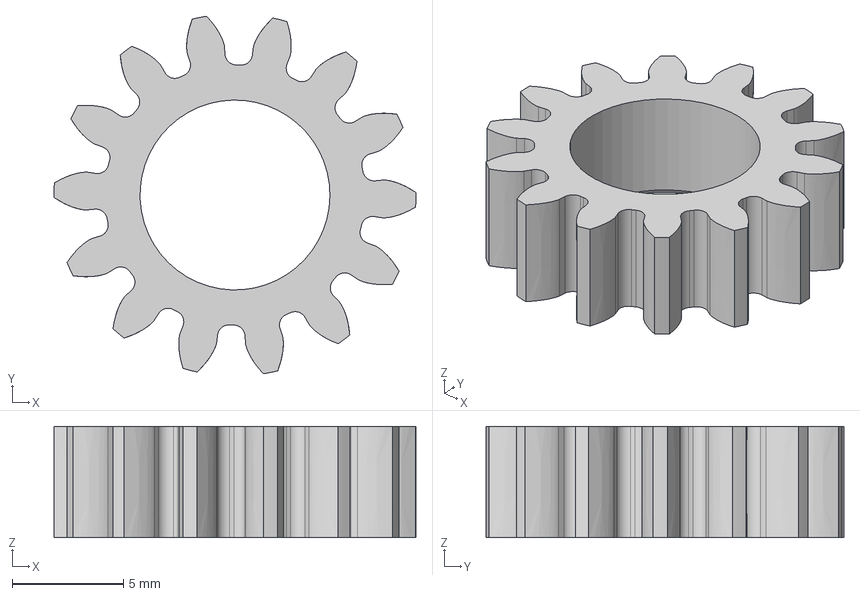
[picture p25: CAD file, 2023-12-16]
BFI Gears/CAD/BFI Main Gear 14 tooth 4X.step
16.3 x 16.1 x 5.00 mm

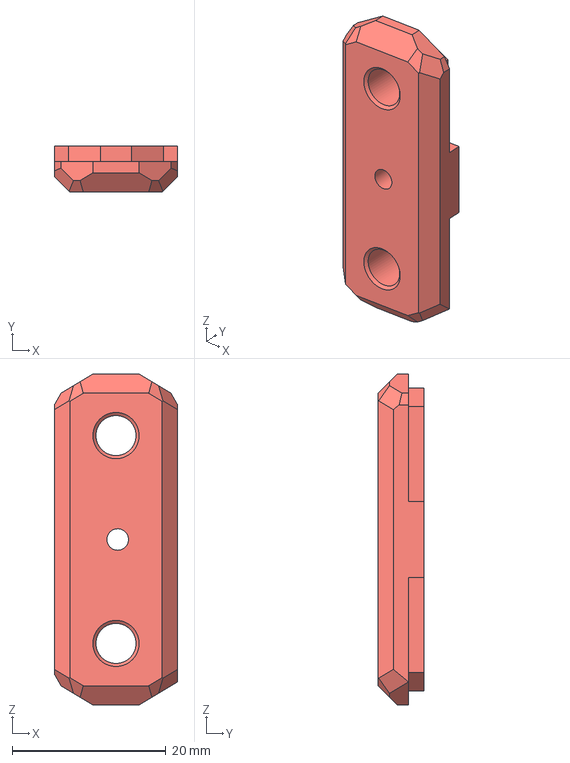
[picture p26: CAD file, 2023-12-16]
BFI Gears/CAD/BFI Gearz Trident Front Cover 2X.step
16.0 x 6.00 x 43.0 mm

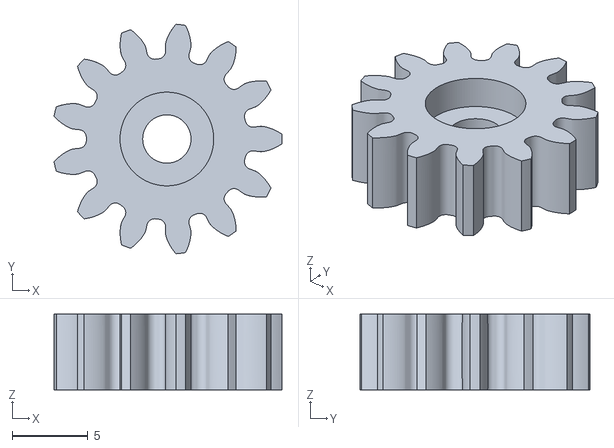
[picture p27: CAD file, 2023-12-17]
BFI Gears/STLs/BFI Gears M3x6 Recessed Idler 2X.stl
15.1 x 15.2 x 5.00

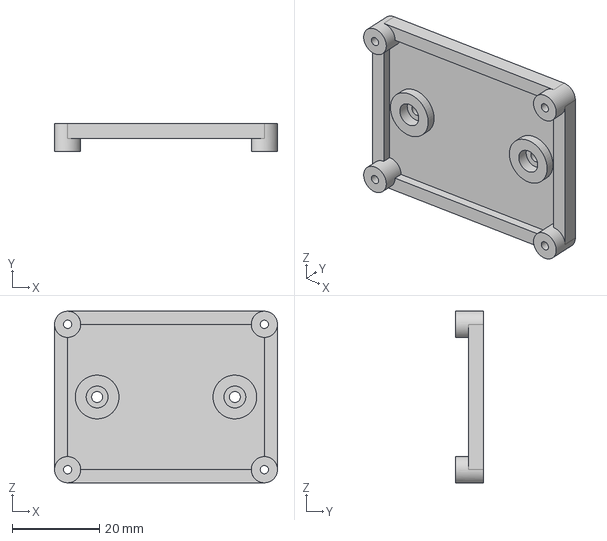
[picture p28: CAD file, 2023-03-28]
DIN Relay Mounts/CAD/DIN relay mount double.step
51.0 x 6.50 x 39.2 mm

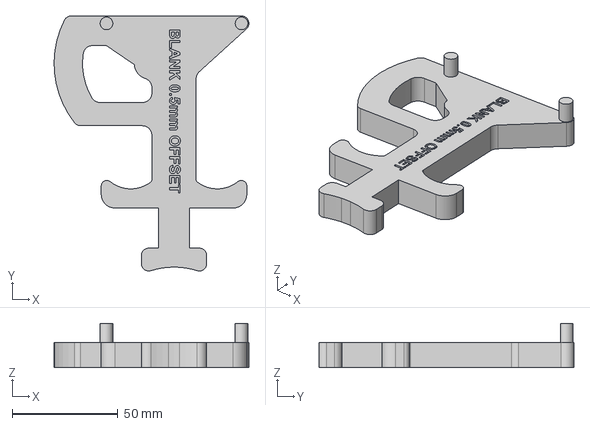
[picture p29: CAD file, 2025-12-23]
GT2 Belt Tension Meter/CAD/Tension Meter Blank 0.5mm Offset.step
92.3 x 120.8 x 21.0 mm

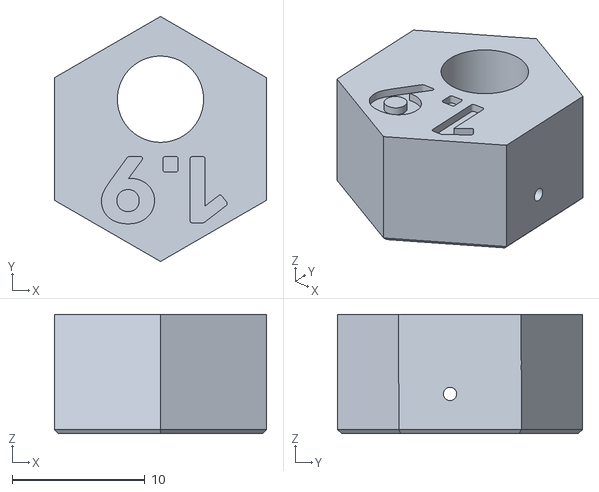
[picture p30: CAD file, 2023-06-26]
GT2 Belt Tension Meter/STLs/GT2 Calibration Wire Pivot 0.032.stl
16.0 x 18.5 x 9.00

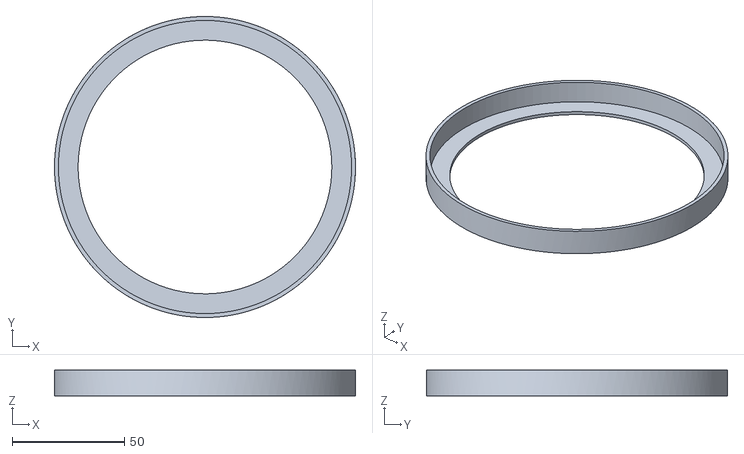
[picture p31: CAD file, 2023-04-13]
Junk Drawer/4 Inch Duct Parts/STLs/Window-Canister Flange Ring 2x.stl
134.1 x 134.1 x 11.5

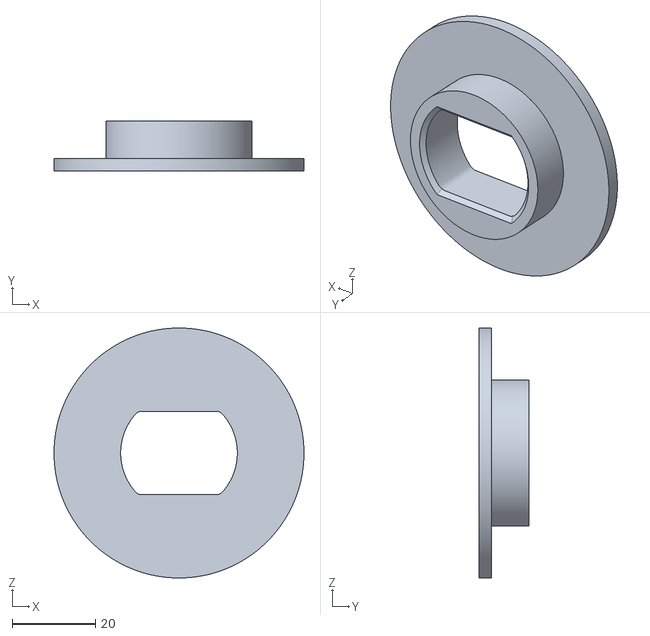
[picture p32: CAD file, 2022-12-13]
Junk Drawer/Glue Holder/STL/superglue holder.stl
60.0 x 12.0 x 60.0

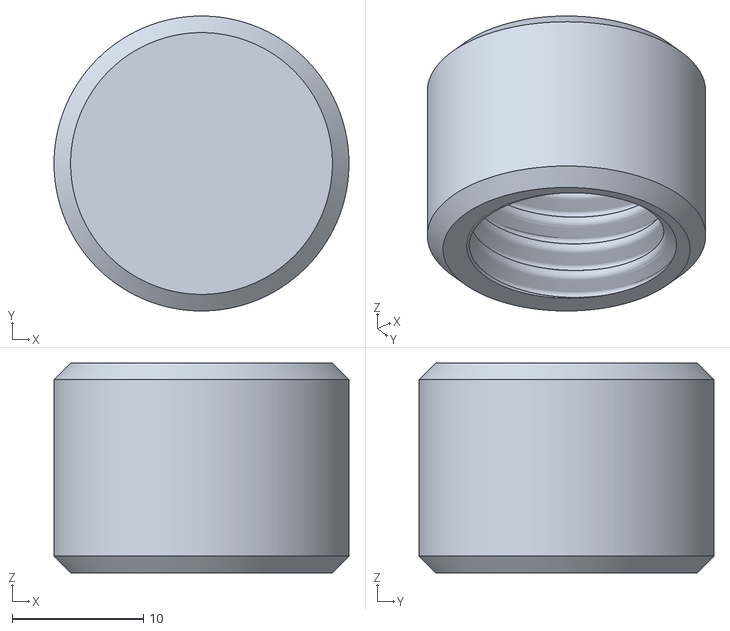
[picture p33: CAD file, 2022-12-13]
Junk Drawer/Mini Dead Blow Hammer/STLs/mini deadblow hammer cap x2.stl
22.5 x 22.5 x 16.0

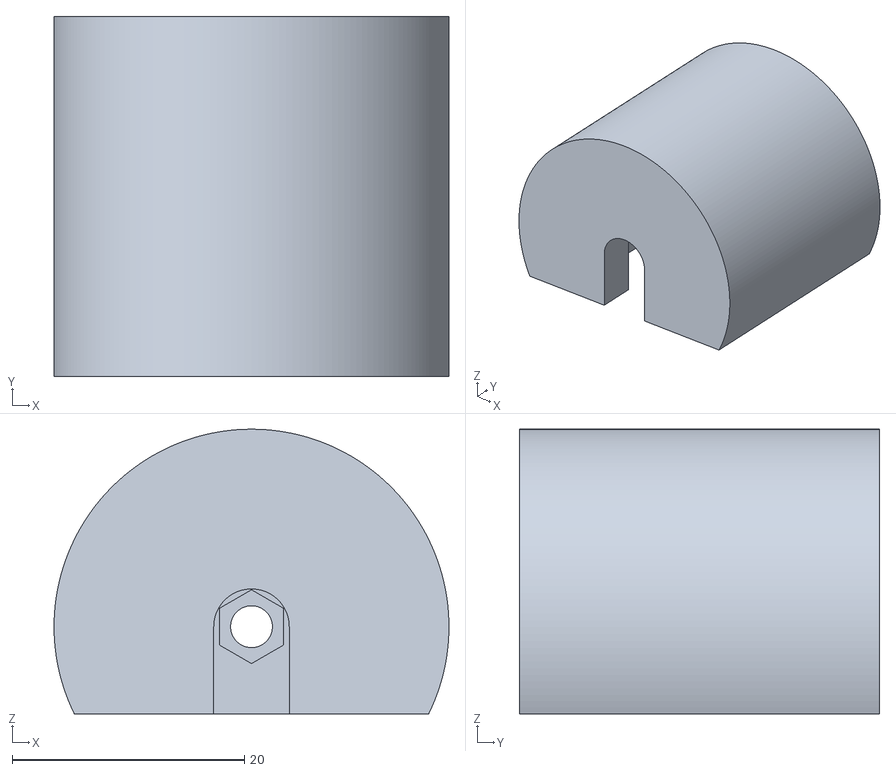
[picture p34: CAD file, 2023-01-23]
Junk Drawer/puller.stl
34.0 x 31.0 x 24.5

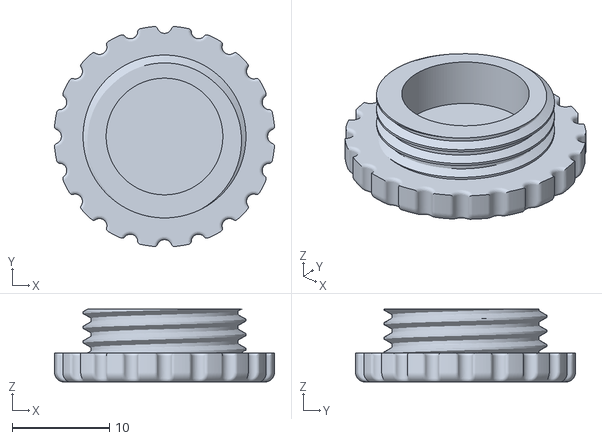
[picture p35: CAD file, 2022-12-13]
Junk Drawer/Step Drill Handle/STLs/Step Drill Handle Cap.stl
22.6 x 22.6 x 7.51

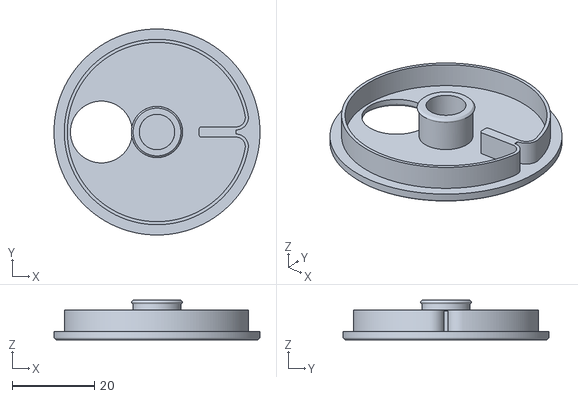
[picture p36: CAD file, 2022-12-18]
LDO ADXL Ribbon Winder/STL Files/winder_lid.stl
50.0 x 50.0 x 9.66

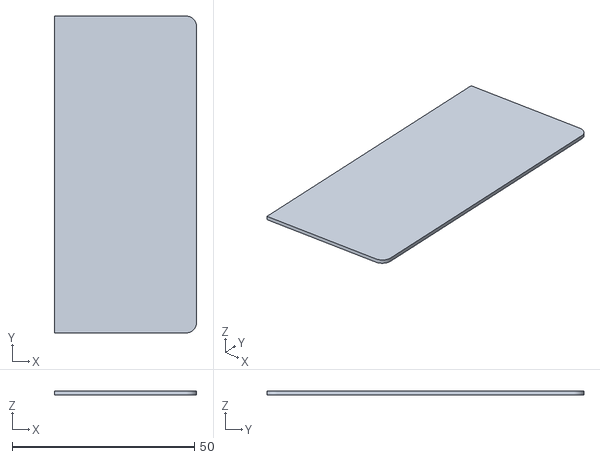
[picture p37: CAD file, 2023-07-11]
Short Stack Bento Filter/STLs/Bento Carbon Catcher2.stl
39.0 x 87.0 x 1.00

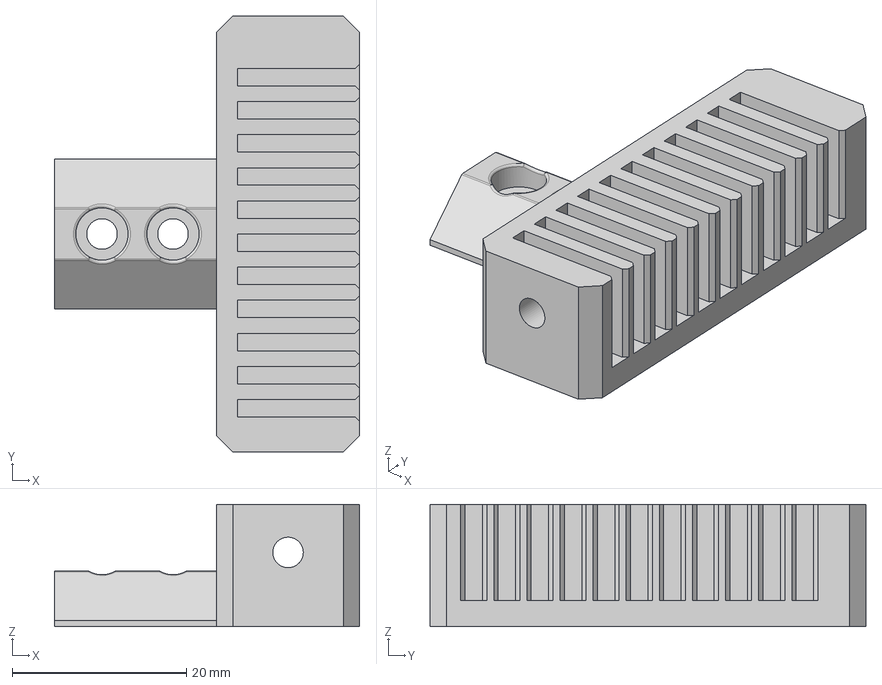
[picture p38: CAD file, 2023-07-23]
Silicone Brush for Decontaminator/CAD/silicone brush holder.step
35.0 x 50.0 x 14.0 mm

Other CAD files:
BFI Gears/STLs/BFI Gears Main 4X.stl
GT2 Belt Tension Meter/STLs/High Tension Gubbins/RC2 HT Calibration Pivot.stl
Silicone Brush for Decontaminator/STL Files/trident_extension_bracket_right_mount.stl
Stealthburner Thermistor Toolheads/STLs/SB_Dragon_TH_Rear_CW2.stl
BFI Gears/CAD/BFI Idler Gear 13 tooth 2X.step
BFI Gears/STLs/BFI GearCap 2X.stl
BFI Gears/STLs/BFI Gears Idler 2X.stl
DIN Relay Mounts/CAD/DIN relay mount single.step
DIN Relay Mounts/STLs/DIN relay mount double.stl
DIN Relay Mounts/STLs/DIN relay mount single.stl
GT2 Belt Tension Meter/CAD/Tension Meter Blank 0.0mm Offset.step
GT2 Belt Tension Meter/CAD/Tension Meter Blank 1.0mm Offset.step
GT2 Belt Tension Meter/STLs/Meter Base-RC2.stl
GT2 Belt Tension Meter/STLs/Meter Slide-RC2 .stl
GT2 Belt Tension Meter/STLs/Needle 00-RC2.stl
GT2 Belt Tension Meter/STLs/Needle 01-RC2.stl
GT2 Belt Tension Meter/STLs/Needle 02-RC2.stl
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

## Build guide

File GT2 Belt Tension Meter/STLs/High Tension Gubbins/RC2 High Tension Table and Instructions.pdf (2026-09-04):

### ALTERNATIVE CALIBRATION TABLE FOR HIGHER TENSION APPLICATIONS

* WARNING: Using these higher values assumes that you know what you are doing and that your printer is equipped with “double shear” supported stepper motors wherein bearings attached to your motor mounts support the motor shaft both above and below the pulley to prevent motor shaft damage.

(*UPPER VALUES FOR USE ON DOUBLE SHEAR MOTOR SETUPS ONLY!)

### HIGHER TENSION - 6mm & 9mm GT2 and GT3

(These values require re-calibrating meter from stock 1.9 value to 1.5 using calibration wire)

STATIC BELT TENSION N (lb) | METER READING (NEOPRENE) | METER READING (EPDM)
8.90 ( 2.0) | 1.2 | 1.3
11.12 (2.5) | 1.4 | 1.5
13.34 (3.0) | 1.7 | 1.8
15.57 (3.5) | 2.0 | 2.1
17.8 (4.0) | 2.2 | 2.3
20.02 (4.5) | 2.3 | 2.4
22.24 (5.0) | 2.4 | 2.5
24.47 (5.5) | 2.5 | 2.6
26.69 (6.0) | 2.6 | 2.7
29.40 (6.5) | 2.7 | 2.8
*31.14 (7.0) | 2.75 | 2.85
*33.36 (7.5) | 2.8 | 2.9
*35.59 (8.0) | 2.85 | 2.95
*37.81 (8.5) | 2.9 | 3.0
*40.03 (9.0) | 2.95 | 3.05
*44.48 (10.0) | 3.0 | **3.1

** approximated tick just past 3 on the dial face.

### ALTERNATIVE HIGH TENSION CALIBRATION INSTRUCTIONS

To get your stock RC2 belt tension meter to register and read up to 10lbs (~44.5N) you can recalibrate it using the same method in the main manual but instead of using the 1.9 value on the meter you will instead increase the preload on the calibration screw (clockwise) until the meter reads 1.5 on the dial face with the calibration wire attached. This will get you to the maximum capability using stock hardware while only sacrificing a small amount of linearity from 9-10lbs (~40-45N)

Three decimal place values are read when the needle lies equidistant between two tick marks on the dial face (e.g., when the needs is directly between the 2.7 and 2.8 tick marks this will be read as 2.75)

Alternate high tension (1.5) calibration pivot that utilizes the same stock wire is available here: High Tension Pivot (https://github.com/Diyshift/3D-Printer/blob/main/GT2%20Belt%20Tension%20Meter/STLs/High%20Tension%20Gubbins/RC2%20HT%20Calibration%20Pivot.stl)

Doc rev. a

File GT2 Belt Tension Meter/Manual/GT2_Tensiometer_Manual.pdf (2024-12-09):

# GT2 Belt Tensiometer

(RC2)

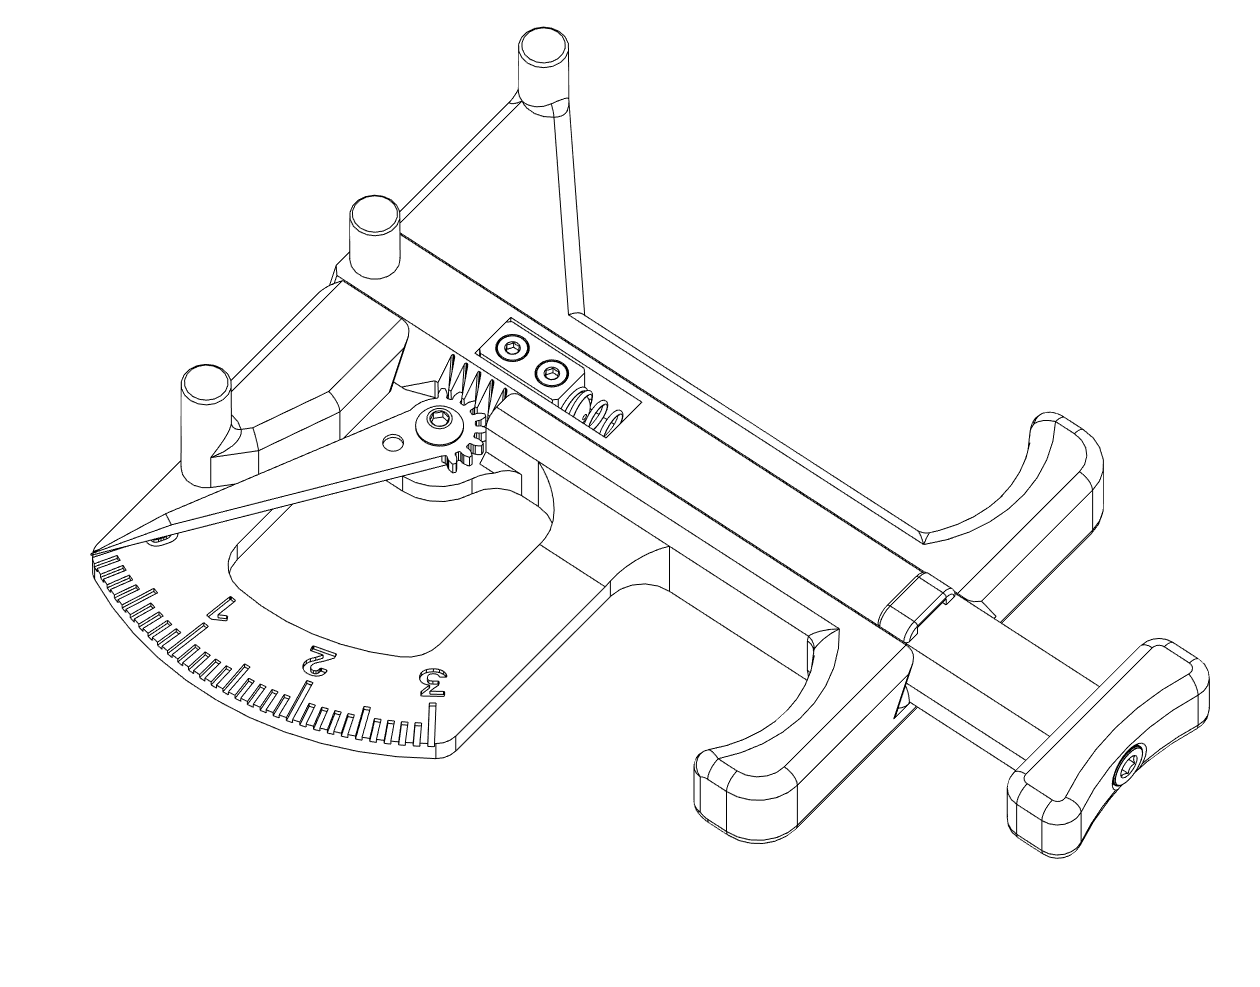
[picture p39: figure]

DETAILS:

This 3D printed tension meter is designed to measure belt deflection to determine belt tension for Gates 6 and 9mm GT2 belts. The goal is to eliminate the need for phone apps that use frequency to determine tension and to provide an easily repeatable number to use when tensioning belts on a 3D printer.

1

TENSION MEASUREMENT FOR A/B BELTS:

1. Refer to your printer's documentation for proper belt tension or refer to the table and references on pages 5-6.
2. Printer should be cold and motors on for this test.
3. Move your toolhead through its complete X and Y travel to set your belts.
4. Center your toolhead on the X axis and then position your Y axis so you have enough belt exposed to fit the tension meter with room on either side, 150mm or more is recommended.
5. Depress plunger and place meter on the belt span so that belt is routed through the gauge pins as shown.


6. Slowly release the plunger and note the reading on the dial. *rocking the meter very slightly fore and aft or lightly “pumping” plunger can help to settle the needle and get an accurate reading.
7. Repeat three times to ensure you are getting consistent readings.

2

8. Adjust belt tension then repeat steps 3-5 until you reach the desired tension (see table below) The A/B belt tensions can affect each other. Tightening one will also tighten the other. Go back and forth adjusting each until they are equal.


9. Home X and Y to seat the belts then repeat steps 2-5 to verify that tension is correct and make followup adjustments as needed.
10. Your belts should now be properly tensioned.

3

TENSION MEASUREMENT FOR Z BELTS:

1. Printer should be cold and motors on for this test.
2. Move your Z axis through its entire range of motion to normalize belt tension.
3. Position your Z axis so that enough belt is exposed to fit the tension meter with a bit of room left on each side. 150mm or more is recommended.
4. The tensioning process for Z belts is the same as A/B. Follow steps 5-9 for A/B instructions substituting Z values until your desired tension is reached and all Z belts are equal.

Note: Depending on your printer your belt tension may increase slightly when utilizing a heated chamber so keep this in mind when selecting tensions in the higher range. When checking tension always remember to run the printer through its full range of travel before measuring to normalize the tension in the belt path.

4

Tension guidelines for tested printers

PRINTER MODEL - BELT | MIN TENSION (meter reading) | MAX TENSION (meter reading)
Voron - A/B (all stock models) | 1.8 (1.9 EPDM) | 2.2 (2.3 EPDM)
Voron 2.4 and Micron - Z | 2.5 (2.6 EPDM) | 2.8 (2.9 EPDM)
Switchwire - “Z” | 1.8 (1.9 EPDM) | 2.2 (2.3 EPDM)
Bambu Lab X1 and P series | N/A | 2.4*
Prusa Mk3 and MK4 | 1.8** | 2.5**
Creality Ender3 | 1.8** | 2.2**

* Based on measurements taken from factory tensioned/calibrated printers.

** Based on common specifications for unsupported NEMA17 stepper motor shaft and community input.

6mm & 9mm GT2 and GT3

STATIC BELT TENSION N (lb) | METER READING (NEOPRENE) | METER READING (EPDM)
8.90 ( 2.0) | 1.8 | 1.9
11.12 (2.5) | 2.0 | 2.1
13.34 (3.0) | 2.1 | 2.2
15.57 (3.5) | 2.3 | 2.4
17.8 (4.0) | 2.4 | 2.5
20.02 (4.5) | 2.5 | 2.6
22.24 (5.0) | 2.6 | 2.7
24.47 (5.5) | 2.7 | 2.8
26.69 (6.0) | 2.8 | 2.9
29.40 (6.5) | 2.9 | 3.0

Common NEMA 17 Stepper Motor Maximum Radial Force Ratings

Distance from Step Motor Flange: | 5mm | 10mm | 20mm
recommended Radial force: | 20N (4.5lb) | 13N (2.9lb) | 9N (2.0lb)
maximum Radial force: | 58N (13lb) | 37N (8.3lb) | 28N (6.8lb)

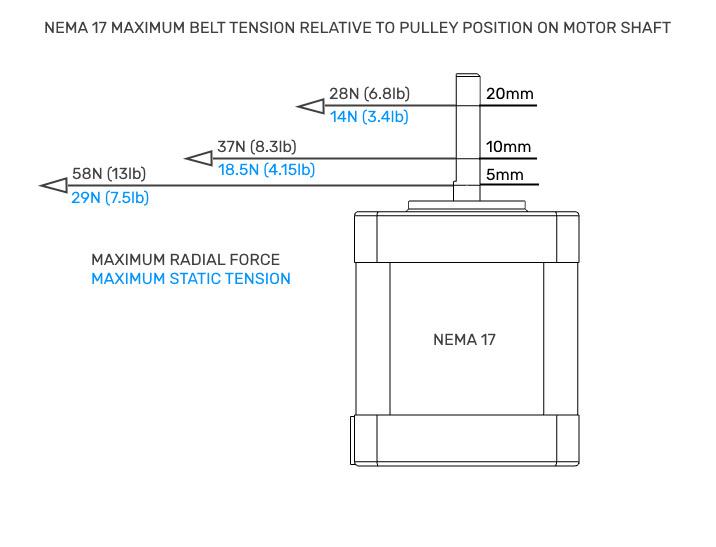
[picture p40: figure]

Radial Force = Static Belt Tension * 2

6

CALIBRATION:

1. Depress plunger and place calibration wire into the jaws making sure the pivot is seated all the way on the left pin as shown. Eye protection is recommended for this step.


2. Release the plunger and note the reading on the dial. Lightly tapping or “pumping” the plunger handle can help to settle the needle and get a better reading.
3. Tighten the screw one turn then depress and release the plunger again. Note that the reading has changed.
4. Repeat steps 3 and 4 until your meter consistently reads 1.9 when checking the deflection of the music wire.
5. Your meter is now calibrated and ready for use.

7

Calibration wire can be stowed on the center pin with wire secured beneath the slides wire keeper.


CARING FOR YOUR METER:

- Protect measurement pins from shock or excessive force. While the pins are designed to to exceed the measurement forces applied by the meter but will break if subjected to excessive force or drops.
- Keep away from harsh cleaners or anything containing acetone as these can damage the ABS plastic.
- No lubrication should be necessary. This design has been tested to several thousand cycles without need for followup lubrication.
- Please try to reuse the shipping box for storage. I did my best to specify a box that could be reused and minimize waste.

8

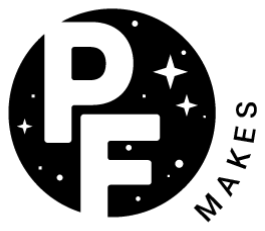
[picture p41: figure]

This work is licensed under the Creative Commons Attribution-NonCommercial-ShareAlike 4.0 International License. To view a copy of this license, visit http://creativecommons.org/licenses/by-nc-sa/4.0/ or send a letter to Creative Commons, PO Box 1866, Mountain View, CA 94042, USA.

Rev. B

9

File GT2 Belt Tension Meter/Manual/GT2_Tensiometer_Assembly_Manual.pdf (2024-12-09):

# GT2 Belt Tensiometer

(RC2)

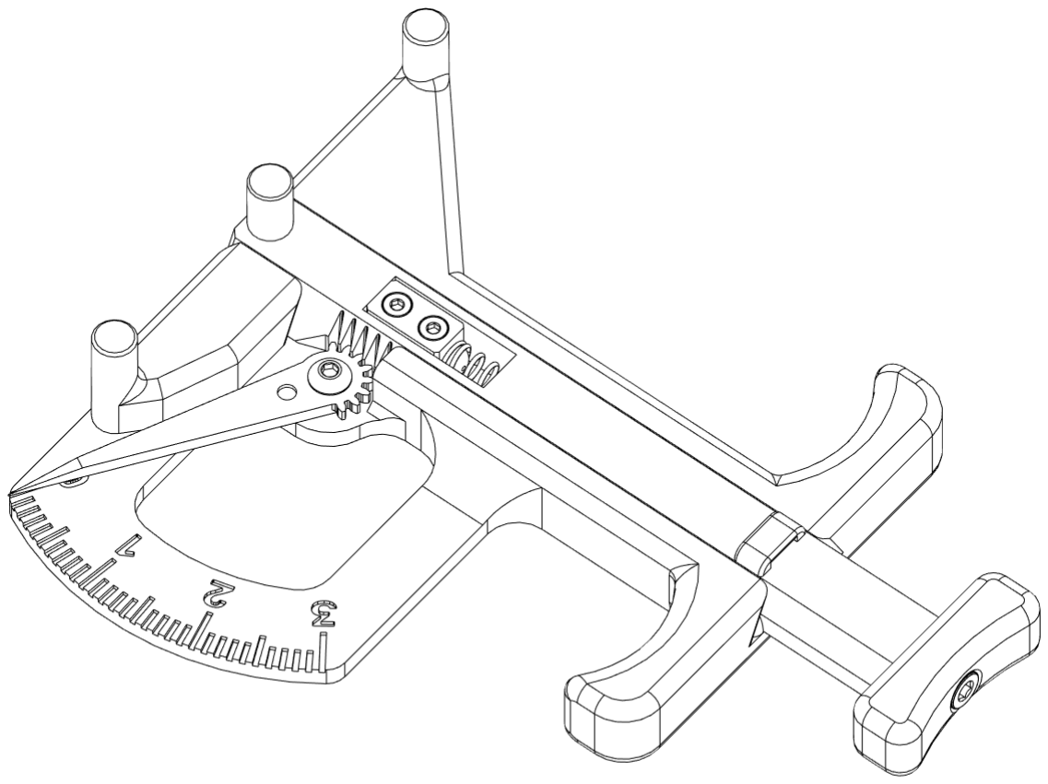
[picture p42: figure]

DETAILS:

This 3D printed tension meter is designed to measure belt deflection to determine belt tension for Gates 6 and 9mm GT2 belts. The goal is to eliminate the need for phone apps that use frequency to determine tension and to provide an easily quantifiable and repeatable number to use when tensioning belts on a 3D printer. The repeatability and accuracy of this meter will be partially dependent on the build quality but you can expect approximately ± 1.0N (0.25lb) accuracy on a carefully built and calibrated meter.

BOM:

- 1x M3x7 Button Head Cap Screw (or M3x6 BHCS if available)
- 1x M3x25 Socket Head Cap Screw
- 1x M3x8x0.6 Washer
- 2x M2x10 Socket Head Self Tapping Screws
- 1x 0.81mm x 100mm (0.032” x 4”) tempered straight steel music wire
- 1x 6mm OD x 0.6mm wire dia. x 50mm free length compression spring with 20 active coils (0.35N/mm spring rate)

TOOLS:

- M3 drill bit and holder
- ABS safe grease such as SuperLube Synthetic or Oatey/Harvey's silicone grease
- 1.5, 2, and 2.5mm hex bit drivers. Ball end hex keys will likely give you a hard time here.
- Toothpicks and Q-tips for applying grease
- Hobby knife (X-Acto)
- Small flat needle file (optional)
- Small triangular smooth cut file (for cleaning up gear teeth and slide channel if needed)
- Cutter capable of cutting hardened music wire (do NOT use your nice flush cutters for this)

PRINT SETTINGS:

- Print in ABS or ASA for best results
- Slide, needles and spring spacer components work best when printed on smooth or satin PEI
- Layer height 0.2mm
- 4 perimeters 5 top and 5 bottom layers
- 40% grid infill

- 0.4mm nozzle with 0.4mm line width throughout
- No seams allowed on needle or slide gear teeth, use blockers or adjust seam settings in your slicer
- Color change at layer 18 for Base and layer 43 Pivot for dual color contrasting text.
- Print one of each needle sizes for ease of assembly/tuning
- Your printer should be well tuned for this project (for example, able to produce a near-perfect Voron cube). Any PA issues or over/under extrusion will likely result in a poorly performing meter

ASSEMBLY:

1. Clean up printed parts as needed. Correct any zits, blobs or other print defects using a small file or hobby knife. Pay special attention to the gear teeth on the slide and needle. Carefully remove any stringing or blobs taking care not to change the tooth profile.
2. Check the fit between the slide and base. It should be loose enough to drop into the base freely without using force.
3. Using a cotton swab, apply a light layer of grease to the spring channel in the shaded area shown below. Do not lubricate the meter Base or Slide dovetail area as stiction may occur causing inaccurate readings.

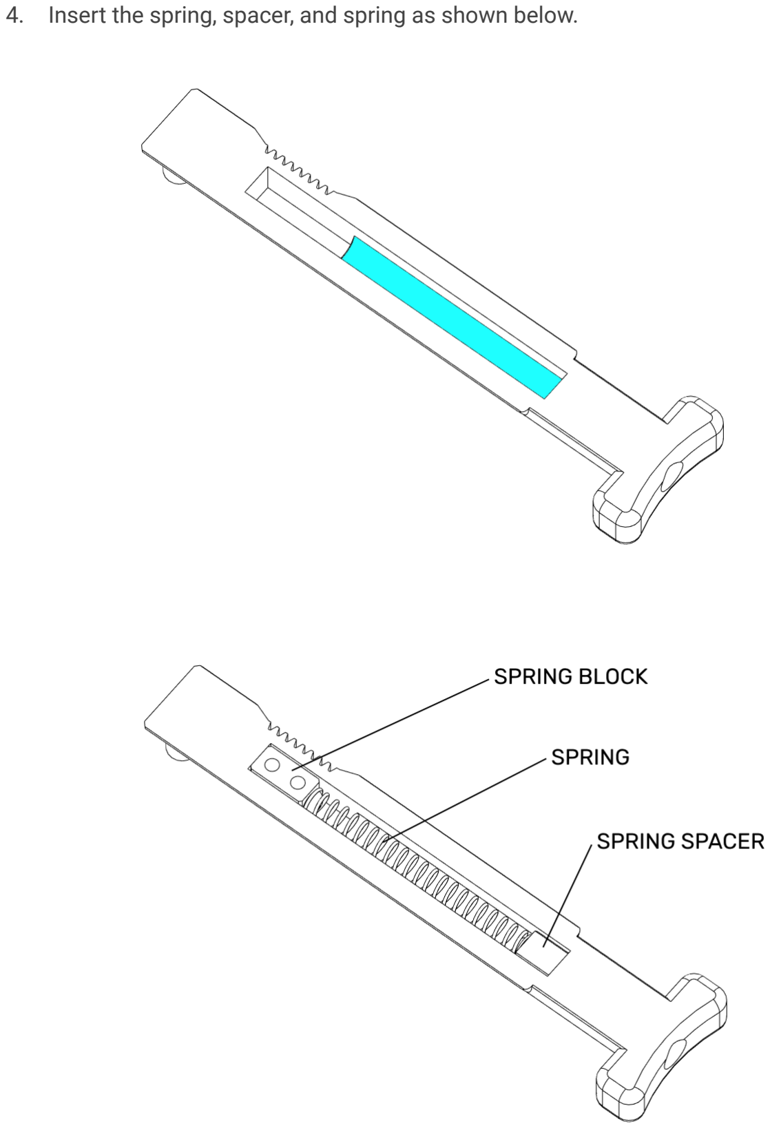
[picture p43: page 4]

4. Insert the spring, spacer, and spring as shown below.

5. Insert the spring spacer, spring and spring block in that order as shown. Note of the position of the counterbores on the spring block, they should be facing down in this step.
6. Flip the assembled slide and carefully insert the slide into the base as shown below. Spring tension should hold the parts in place.

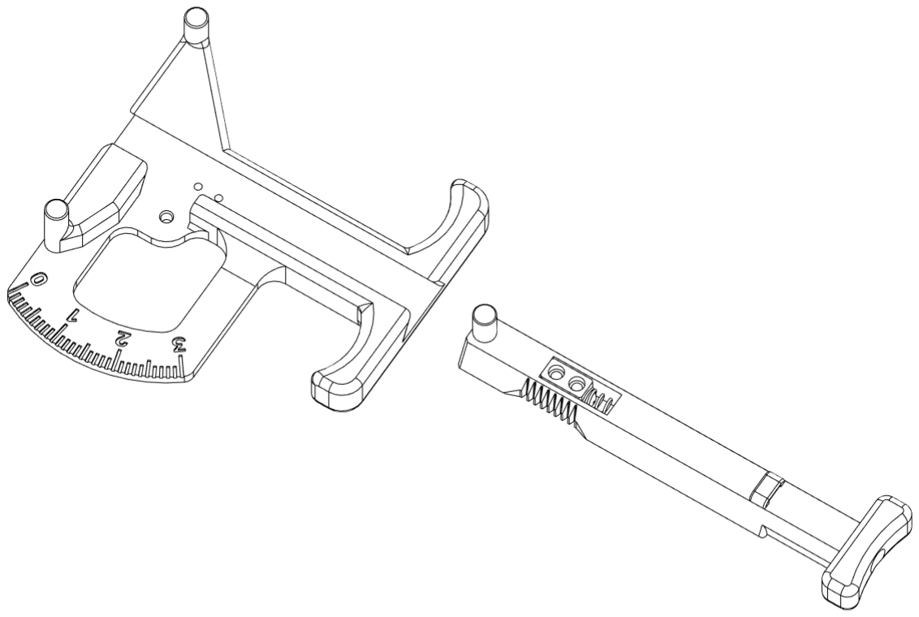
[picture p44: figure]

7. Align the slide with the front of the base so that they are flush and the two holes in the spring block are aligned with the corresponding holes in the base.
8. Secure the spring block to the base using two self-tapping M2 screws.

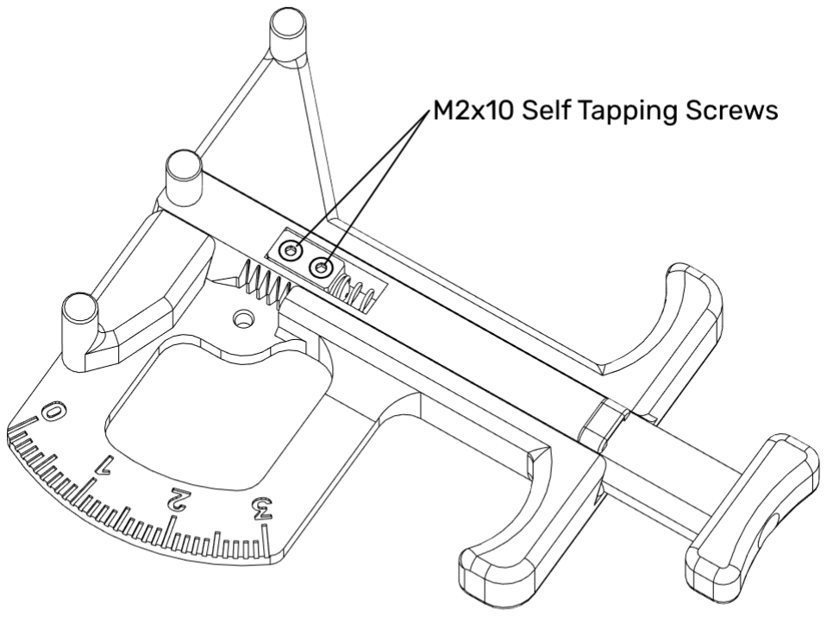
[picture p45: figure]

9. Depress slide plunger to check that the slide is moving smoothly and without binding.
10. Starting with a #2 needle use trial and error to determine the needle with the best fit. When aligned on the hole, the needle’s teeth will mesh with the slide’s teeth. The two holes should be close to concentric.

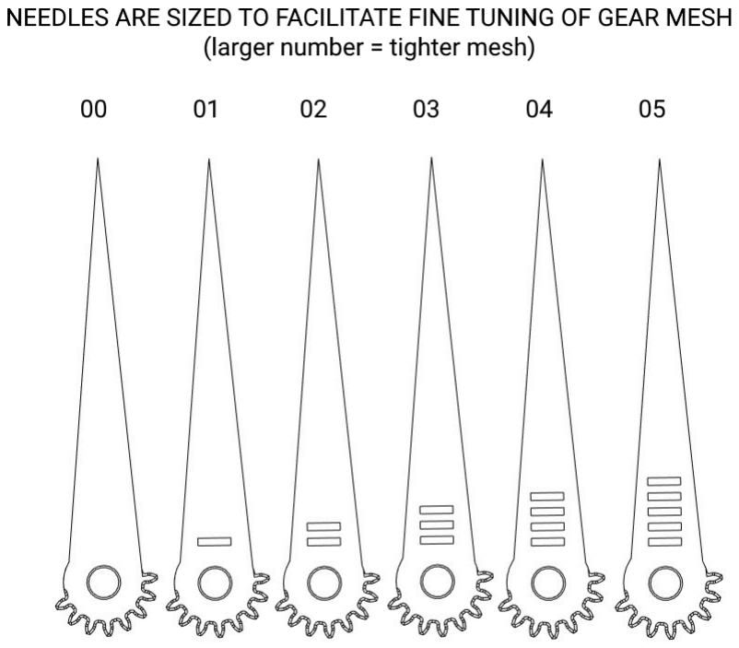
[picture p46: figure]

(Bottom view of needles showing sizing markers)

11. Ream the hole in the needle with a 3mm drill bit and check the fit using the M3x25 SHCS screw. The needle should rotate freely under its own weight. (tip: if you don’t own a 3mm drill bit you can use the M3x25 screw to ream the hole by screwing it into the needle and intentionally stripping the threads)
12. Insert the M3x6 BHCS through the top of the needle (as denoted by the circular stamp).
13. Place the M3x8 washer onto the base, aligning it with the hole with the smoothest side up. (some washers have a burr from stamping, this should face down for best result)

14. Secure the needle onto the washer with the M3x7 BHCS, making sure the needle aligns to the zero position and the round divot is facing up.

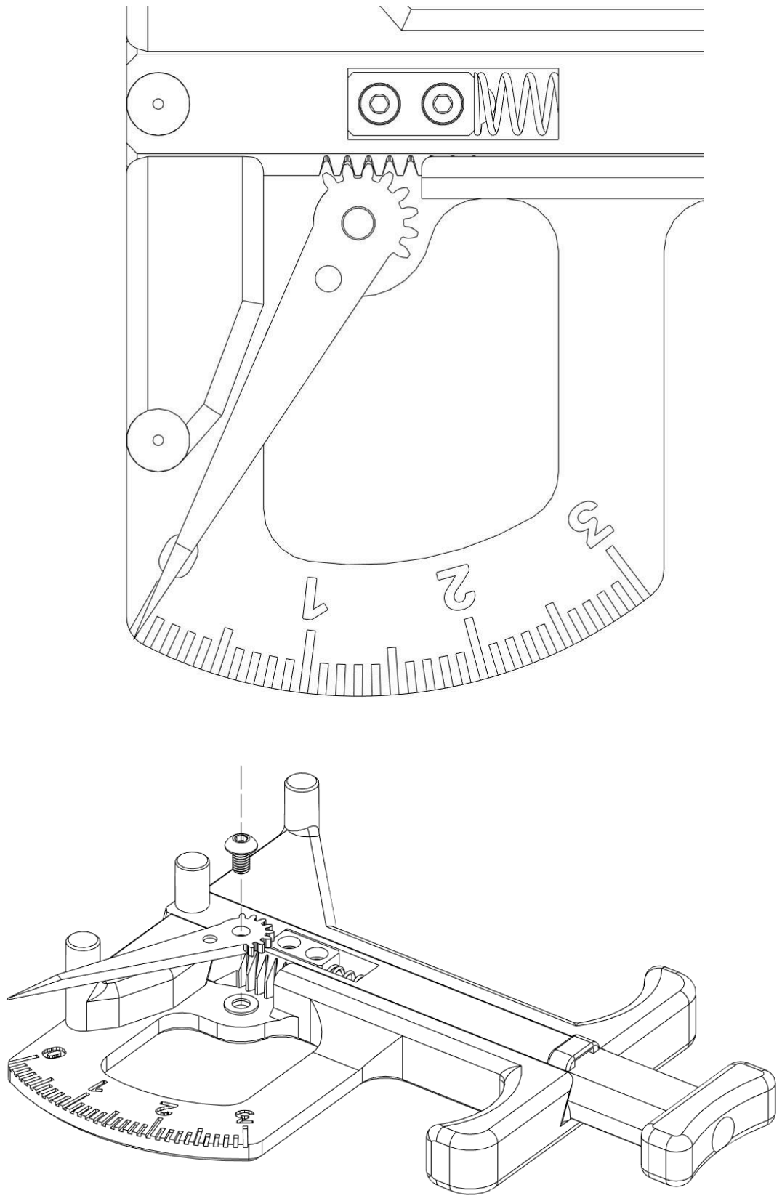
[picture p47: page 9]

15. Tighten screw until just snug then back off in small increments until the needle moves freely.
16. Depress the slide’s plunger several times to ensure that the needle moves freely without jumping or binding.
17. Check the needle’s backlash by gently wiggling with a finger. If the needle moves more than one tick on the dial, swap to the next size up and repeat this test. You want a needle size that gives you the least amount of backlash while still allowing smooth motion of the slide.
18. Once you have the correct needle selected, use a toothpick or similar to apply a very small amount of grease to the areas shown below.
19. Test to confirm that the needle spins freely on the screw.

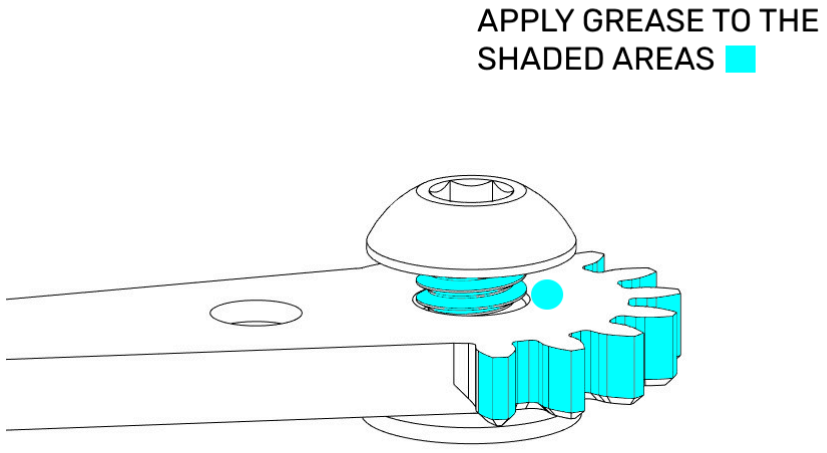
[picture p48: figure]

20. Flip the needle over and apply a very light layer of grease to the area that contacts the M3x8 washer, being careful not to get any on the lower threads.

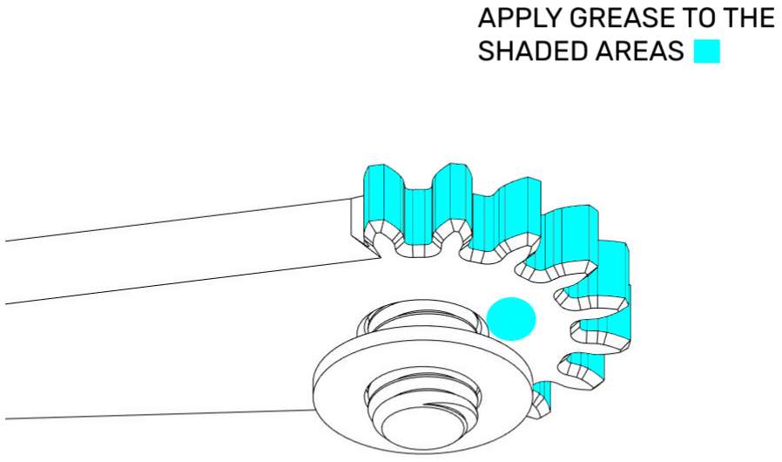
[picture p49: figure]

21. Apply a small amount of grease to the teeth on the needle as shown..
22. Place the M3x8 washer onto the base.
23. Again, tighten the screw until just snug then back off until the needle swings freely.
24. Cycle the slide 20-30 times to make sure grease is distributed and the gears mesh.
25. Slowly cycle the slide several times and observe the needle’s motion. It should be smooth throughout its entire range with no sticking or jumping. Adjust screw securing needle as needed to facilitate free movement.
26. Finally, install the M3x25 SHCS preload screw into the slide plunger as shown. This screw is threaded into plastic. Tighten until the head is flush with the plunger. Your meter is now assembled and ready for calibration.

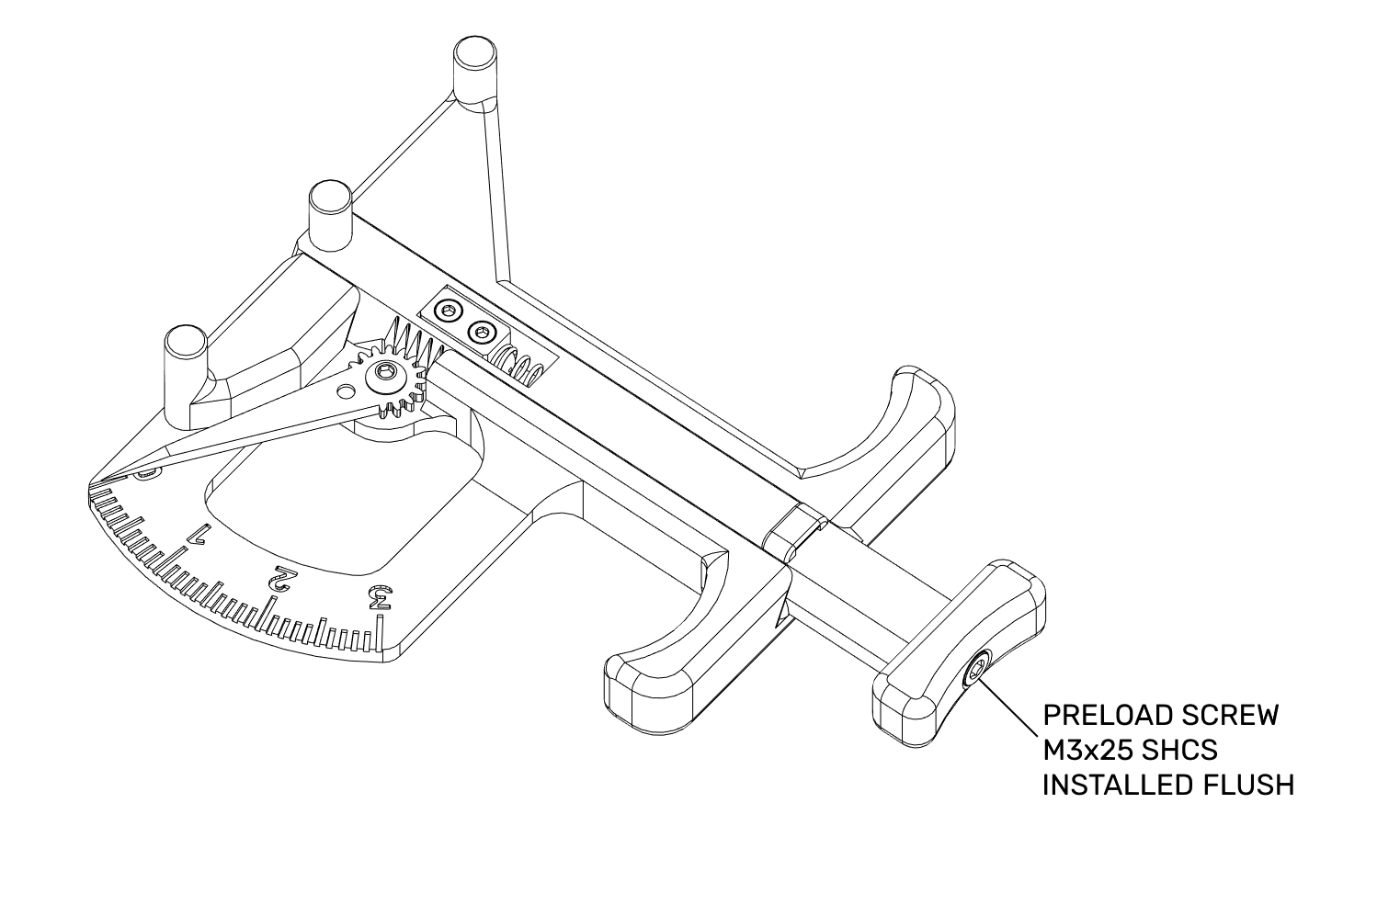
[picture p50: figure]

*Note: If your meter dial is not resting on the zero mark you may need to loosen the two self tapping screws in the spring block to adjust.

CALIBRATION:

1. Cut music wire to 100mm and deburr the ends with a file. (note: do not use your good side cutters for music wire, dremel cutoff or hard wire cutter
recommended)
2. Glue the wire into the hole on the side of the calibration handle making sure it is fully seated and flush on the opposite side. Afterwards remove any burrs or glue from the hole in the calibration pivot. It should rotate freely on the left pin when

installed.

3. Depress plunger and place calibration wire into the jaws making sure the pivot is seated all the way on the left pin as shown. Eye protection is recommended for this step.

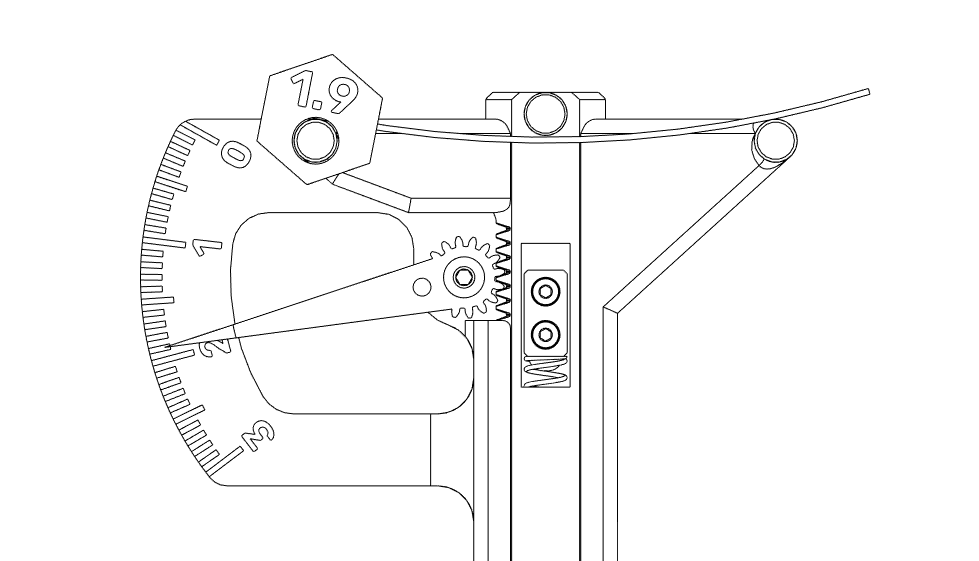
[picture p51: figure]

4. Release the plunger and note the reading on the dial. Lightly tapping or “pumping” the plunger handle can help to settle the needle and get a better reading.
5. Tighten the preload screw in the back of the plunger one turn then depress and release the plunger again. Note that the reading has changed.
6. Repeat steps 3 -5 until your meter consistently reads 1.9 when checking the deflection of the music wire.

7. Your meter is now calibrated and ready for use.

ALTERNATIVE CALIBRATION:

- If straight tempered music wire is not available a suitable weight and spare section of belt can be used. A gallon plastic water jug and scale works well for this. Do not trust weights marked on fitness equipment, weigh them first.
- Suspend a 1.36Kg (3lb) weight from a 250mm section of GT2 belt and measure the tension with the belt teeth in contact with the two outer pins on the meter as shown below in step 3.
- Adjust the preload screw as needed until the meter reads consistently across several measurements. 2.1 for standard rubber or 2.2 EPDM high temperature belt.

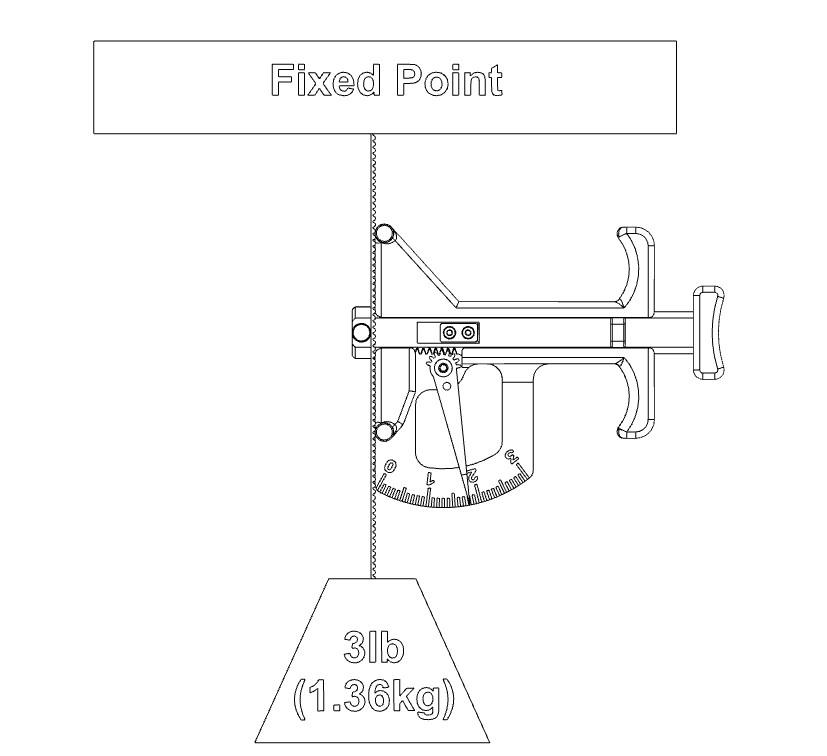
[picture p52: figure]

Calibration wire can be stowed on the center pin with wire secured beneath the slides wire keeper.

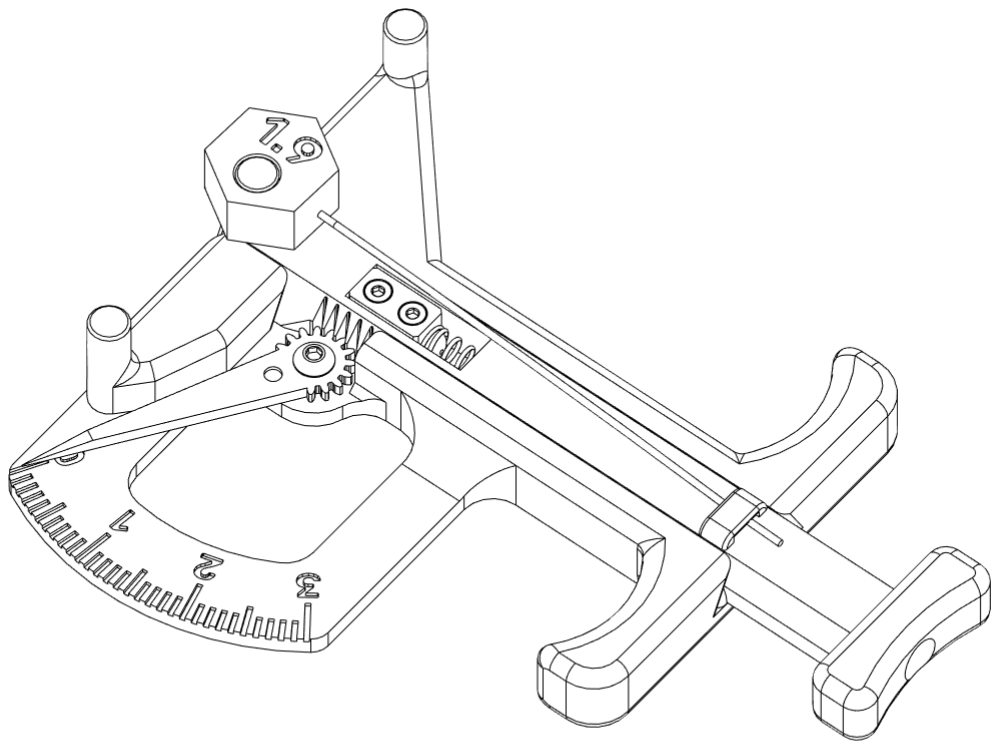
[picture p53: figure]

TENSION MEASUREMENT A/B BELTS:

1. Refer to your printer's documentation for proper belt tension or see table below
2. Issue G28 to home printer. Printer should be cold for this test.
3. Center toolhead on X and then move Y until the X/Y idler centers are 150mm from the front idler centers. Motors should be on for this test. (note: unlike phone apps the 150mm distance is not a critical distance just a way to ensure that the toolhead is centered and to aid in obtaining repeatable results)

4. Depress plunger and place meter on the 150mm belt span so that belt is routed through the gauge pins as shown.

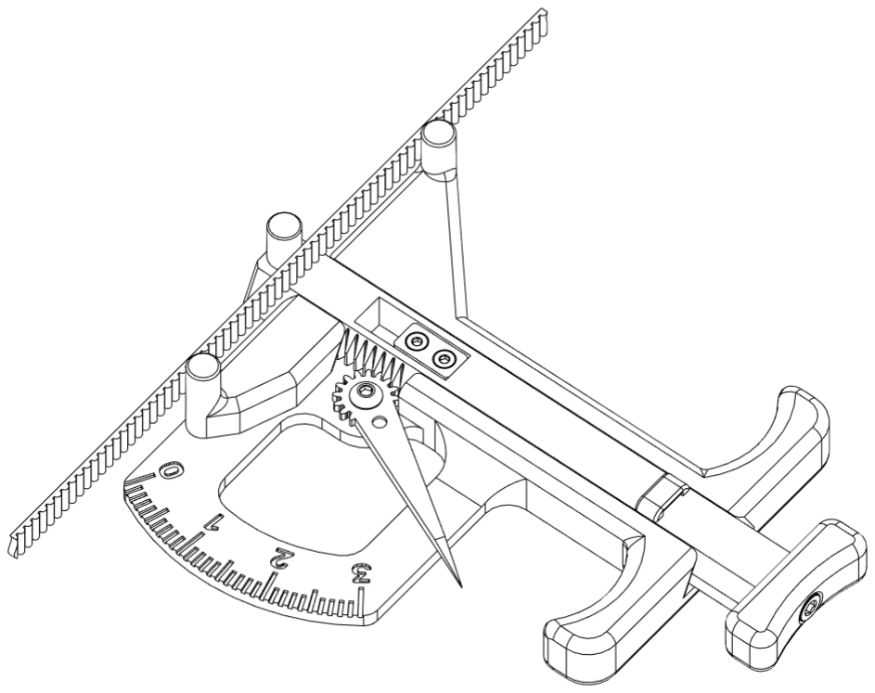
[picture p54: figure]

5. Slowly release the plunger and note the reading on the dial. *rocking the meter very slightly fore and aft or lightly “pumping” plunger can help to settle the needle and get an accurate reading.
6. Repeat three times to ensure you are getting consistent readings.
7. Adjust belt tension then repeat steps 3-5 until you reach the desired tension (see table below) The A/B belt tensions can affect each other. Tightening one will also tighten the other. Go back and forth adjusting each until they are equal.

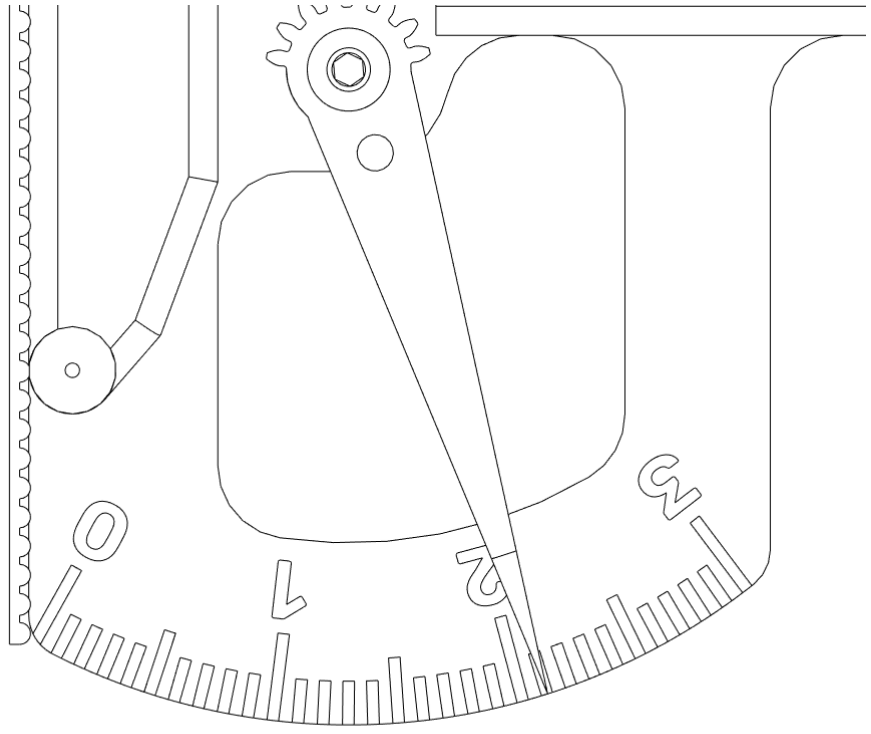
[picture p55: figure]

8. Home X and Y to seat the belts then repeat steps 2-5 to verify that tension is correct and make followup adjustments as needed.
9. Your belts should now be properly tensioned.

Note: Depending on your style of printer your belt tension may increase slightly when utilizing a heated chamber so keep this in mind when selecting tensions in the higher range. Check your belts after a preheat to be sure you are not exceeding safe limits. When checking tension always remember to run the measured axis through its full range of travel before measuring to normalize the tension in the belt path.

Tension guidelines for tested printers

PRINTER MODEL - BELT | MIN TENSION (meter reading) | MAX TENSION (meter reading)
Voron - A/B (all stock models) | 1.8 (1.9 EPDM) | 2.2 (2.3 EPDM)
Voron 2.4 and Micron - Z | 2.5 (2.6 EPDM) | 2.8 (2.9 EPDM)
Switchwire - “Z” | 1.8 (1.9 EPDM) | 2.2 (2.3 EPDM)
Bambu Lab X1 and P series | N/A | 2.4*
Prusa Mk3 and MK4 | 1.8** | 2.5**
Creality Ender3 | 1.8** | 2.2**

* Based on measurements taken from factory tensioned/calibrated printers.

** Based on common specifications for unsupported NEMA17 stepper motor shaft and community input.

6mm & 9mm GT2 and GT3

STATIC BELT TENSION N (lb) | METER READING (NEOPRENE) | METER READING (EPDM)
8.90 ( 2.0) | 1.8 | 1.9
11.12 (2.5) | 2.0 | 2.1
13.34 (3.0) | 2.1 | 2.2
15.57 (3.5) | 2.3 | 2.4
17.8 (4.0) | 2.4 | 2.5
20.02 (4.5) | 2.5 | 2.6
22.24 (5.0) | 2.6 | 2.7
24.47 (5.5) | 2.7 | 2.8
26.69 (6.0) | 2.8 | 2.9
29.40 (6.5) | 2.9 | 3.0

31.14 (7.0) | 3.0 | N/A

Common NEMA 14 & 17 Stepper Motor Maximum Radial Force Ratings

DISTANCE FROM STEPPER MOTOR FLANGE | 5mm | 10mm | 20mm
recommended Radial force: | 20N (4.5lb) | 13N (2.9lb) | 9N (2.0lb)
maximum Radial force: | 58N (13lb) | 37N (8.3lb) | 28N (6.8lb)

Radial Force = Static Belt Tension * 2


KITS:

- Complete Hardware Kits (https://www.etsy.com/listing/1508474957/hardware-kit-for-diy-3d-printer-belt?click_sum=25d1381a)
- Complete Assembled and Calibrated Meters (https://www.etsy.com/listing/1508462271/belt-tension-meter-for-3d-printers?click_sum=d5bdfbd0&frs=1)

HARDWARE SOURCES:

- Spring (https://www.amazon.com/dp/B076LTYY5K?psc=1&ref=ppx_yo2ov_dt_b_product_details)
- Music Wire (https://www.amazon.com/gp/product/B002WXGIHC/ref=ppx_yo_dt_b_search_asin_title?ie=UTF8&psc=1)
- Superlube Synthetic Grease (https://www.amazon.com/Super-Lube-21010-Grease/dp/B005R2NIIC) Tested NGLI 0 through 2
- Harvey's Silicone Grease (https://www.amazon.com/Wm-Harvey-050090-C-Silicone-Grease/dp/B000FPANUW)

REFERENCE:

- Stepper Info (http://ldomotors.com/products/show/42mm-hybrid-stepper-series)
- Belt Tension Calculators (https://www.clavis.co.uk/belt-calculator/)
- Spring Rate Calculator (https://www.acxesspring.com/compression-spring-calculations.html)

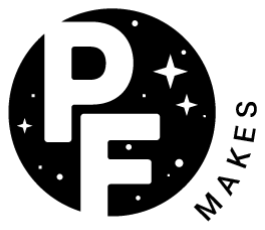
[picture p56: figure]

Manual Rev.G

This work is licensed under the Creative Commons Attribution-NonCommercial-ShareAlike 4.0 International License. To view a copy of this license, visit http://creativecommons.org/licenses/by-nc-sa/4.0/ or send a letter to Creative Commons, PO Box 1866, Mountain View, CA 94042, USA.

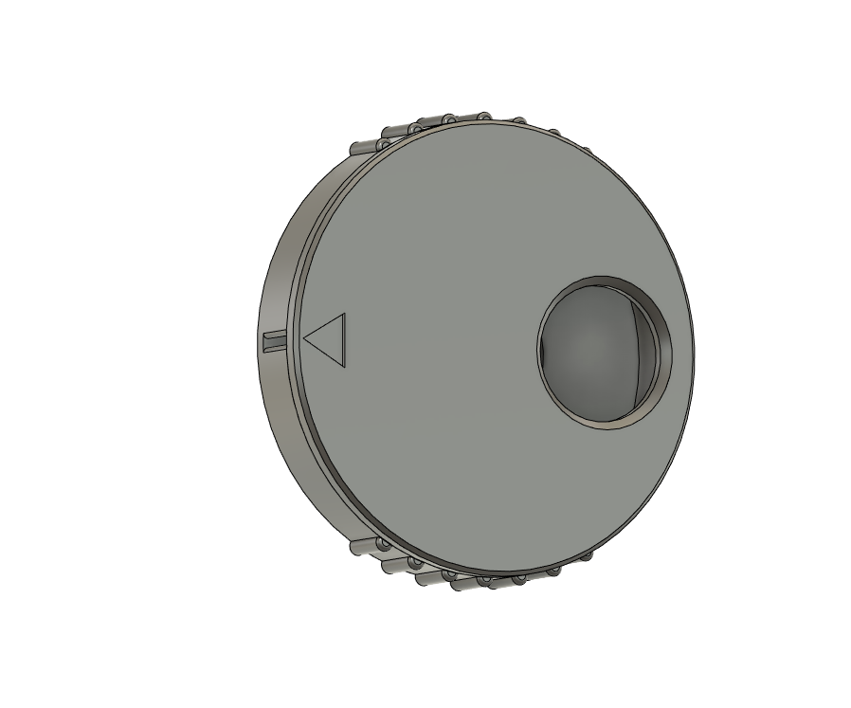
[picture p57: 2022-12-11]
LDO ADXL Ribbon Winder/Images/winder assembled.png

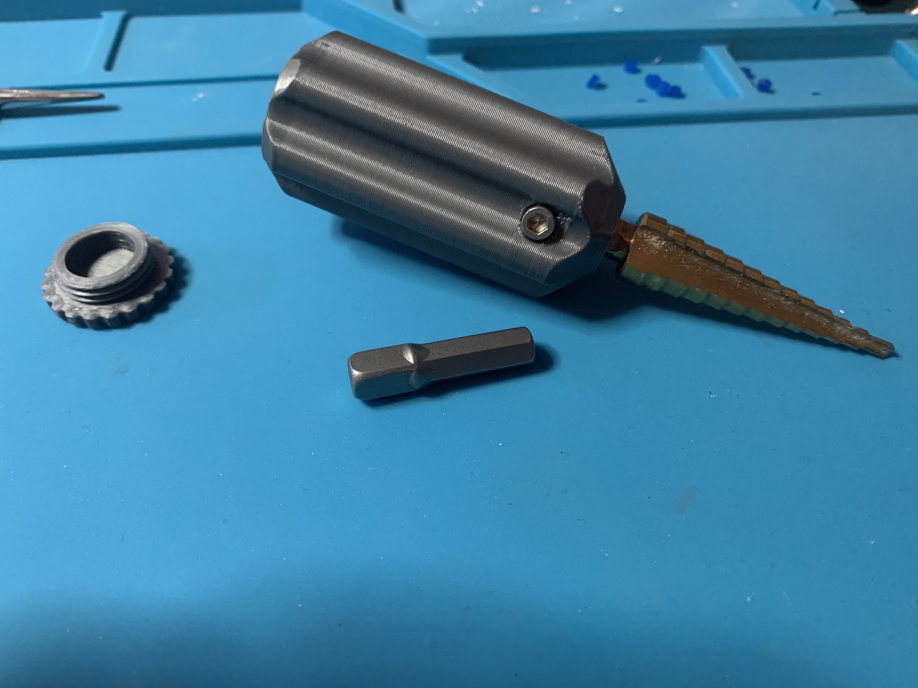
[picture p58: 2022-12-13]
Junk Drawer/Step Drill Handle/Images/step drill handle.jpeg

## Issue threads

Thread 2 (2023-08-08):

GT2 Belt Tension Meter

skyaee, 2023-08-08:
Hello, ALTERNATIVE CALIBRATION, is there any picture demonstration, and the operation method of text writing, I don't quite understand, thank you.

Diyshift, 2023-08-14:
Image added to instructions. let me know if this helps clarify the instructions.

skyaee, 2023-08-15:
> 图像已添加到说明中。让我知道这是否有助于澄清说明。图像已添加到说明中。让我知道这是否有助于澄清说明。

Thank you very much, the pictures are self-explanatory. very helpful.

Closed 2023-08-15.

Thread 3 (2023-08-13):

Trident Thermistor Corner: Broken CAD file

mjonuschat, 2023-08-13:
It looks like the STEP file for the Trident thermistor foot didn't upload correctly, shows as 1 byte sized / empty file.

Diyshift, 2023-08-15:
Thank you for the heads up! Searching for CAD and will post up as soon as I locate the missing file.

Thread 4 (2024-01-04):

Feature request

Tutankamon00, 2024-01-04:
Please add 12mm GT2 belts version, thank you

kot0005, 2024-03-11:
what is the recommended tension for 9mm belts ?

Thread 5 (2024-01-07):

BFI gears incorrect bolt type

EricZimmerman, 2024-01-07:
readme says

`Glue two larger gears to the heads of your M5x40 BHCS using superglue`

but they are SHCS and should be M5x30 from what i can tell

Diyshift, 2024-01-08:
Thanks for the heads up! You are correct the main screws for Trident are indeed SHCS. Should be 40mm length for trident. 30mm BHCS would be for V2 according to the BFI git.

EricZimmerman, 2024-01-08:
I am on a 2.4. Very nice mod.

Closed 2024-01-28.

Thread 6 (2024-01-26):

GT2 Tension Meter - Increase Number/Tick Mark Depth?

awickham10, 2024-01-26:
Would it be possible to make the numbers and tick marks a little deeper? When doing a filament swap, it seems like the three layers or whatever isn't quite enough to get a good color. You can the color mismatch on West3D's page. Awesome project - I'm excited to give it a shot!

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

Diyshift, 2024-01-29:
Thanks for reaching out!
You can probably disregard that image as it is an older version. The one pictured was using a translucent green wich I do not recommend. West 3D has since come out with their own Ambrosia ASA line and it much better in this and almost every other regard, this is what is used in all current production meters for West 3D.  I have included a shot of the current meters in  Ambrosia green.
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

When I tried deeper lettering it decreased the viewing angle so this was kind of a sweet spot for coverage and view angle.

-PF

awickham10, 2024-01-29:
I experienced the same thing with KVP Voron Red, but your point about the viewing angle is probably way more important than the color not matching 😂

Consider this one closed!

Closed 2024-01-29.

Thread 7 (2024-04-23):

Why 70 Duro

cromine11, 2024-04-23:
I was looking into the calculators and I was wondering why you chose 70 Duro. From what I found 50 Duro was in the weight range for my 300 Trident. Did you do testing on the others and found this had the best results?

Diyshift, 2024-04-23:
I got stiffer than spec due to the fact that there is a lot of moving mass up high didnt want the machine shaking violently and it ended up working out.  50 may work but they are pretty soft. Other users have experimented going a step down for their printers eg: 30 duro for a V0 and it ended up being too soft so 50 was the sweet spot for them despite being harder than spec. So I believe that for certain applications the durometer should be chosen based on the application AND weight as opposed to just weight alone. They have excellent calculators here if you really want to go down the rabbit hole ; )   https://www.sorbothane.com/technical-data/design-guide-calculators/vibration-calculator/

Closed 2024-06-09.

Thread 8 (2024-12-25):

Does any 0.81mm steel piano wire work?

Boerny41, 2024-12-25:
The one requested here is hard to get for me, the kits are as well. I'd spend ~$20 on shipping no matter what, and therefore wondered if any piano wire with 0.8 mm diameter will work.

pixelmagic66, 2024-12-31:
Also same issue here (EU) and asking myself the same thing.

Diyshift, 2024-12-31:
Hi,
I have only been able to source the wire listed in the git to test however you can verify it by using the alternate calibration instructions in the git manual using a suspended weight from a section of belt.  If the music wire is hardened and came in a straight pack the 0.8mm and hardened it should be very close.  You will want to use caution with  the coiled stuff as being bent would likely cause a bias in the wire that would be reflected in the deflection read by the meter.  If you do end up calibrating the meter using the alternate method but your wire reads off you can "adjust" the calibration wire by very carefully bending it right where it exits in very small increments to bring it into spec (1.9) so that you can then use the wire for any subsequent calibration.  That being said, of all of the meters I have built  including the original first articles used for hundreds of tests I have yet to have one need a followup calibration even after a year of use.  YMMV but it seems that the meter is able to hold calibration for quite a long period of time following initial post-build calibration.

If you do manage to find a wire that matches the manual calibration method please let me know and I will get it added to the git.

Thanks for reaching out and I hope this helps!

-PF

Diyshift, 2024-12-31:
I will leave this open in case anyone finds an alternate wire in the EU.  Otherwise the vendors below often have kits in stock:

https://viperworx.uk/product/hardware-kit-belt-tension-meter-by-pf-makes?v=0b3b97fa6688

https://www.3dptronics.com/voron-mods/gt2-belt-tension-meter-hardware-kit-by-pf-makes

https://3dkatten.se/en/products/pf-makes-spanningsmatare-hardvarukit

qw3rtn, 2025-05-06:
I ordered this kit:
https://www.replimat.eu/gt2-belt-tension-meter-hardware-kit-by-pf-makes/rt10204

The spring is not listed on the BOM, but was included in the package ;)

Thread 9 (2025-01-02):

Remixed Model Files

Ken6432, 2025-01-02:
I have ordered the belt meter parts kit from West3D and am getting ready to print the parts.  I see a remix on Printables that uses bearings. (https://www.printables.com/model/634190-gt2-belt-tension-meter-wbearings/files).  Is there any reason not to use this instead of your files?  I like the idea of the lower friction design, but if you think I should stick with your original design, I will.  Thanks!

Diyshift, 2025-01-03:
Hi,

I would recommend the version on my git for several reasons. First the bearings while a good idea for some sliding applications are not really needed here as when properly printed and cleaned up. The issue with bearings is that they are only as good as the surface that they are rolling on (printed), In the design you mentioned this includes a supported overhang which could prove problematic. The slide on the stock design should experience very little if any friction when actively measuring tension as it free-floats in the dovetail channel. When building just ensure that the slide drops through vertically under its own weight as depicted in the instructions.

The second and more critical issue involves using a rounded spring spacer which I found in early testing can lead to torsional forces applied to the compression spring when setting your preload. This led to sporadic inaccuracies as it can change spring rate when wound up and let loose later. I intentionally mitigated this by changing the shape so that the spring spacer cannot rotate in the spring channel when the preload screw is installed and adjusted ensuring a constant spring rate and overall length.

I hope this answers your question. The version on my Git is the culmination of months of designing and testing many iterations to get to a design I was confident enough to release for beta and then finally to the public.

If you have any further questions please let me know and I will be happy to answer.

Happy tuning!

-PF

Ken6432, 2025-01-03:
Thanks for the clear, understandable response.  Being a design engineer myself it all sounds very logical and reasonable.  I understand how much effort goes into a design behind the scenes that can make a large amount of difference.  We'll see how the printing goes.  I may be back later

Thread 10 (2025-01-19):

CAD / F3D files?

johnnyphive, 2025-01-19:
Any chance of you sharing / releasing  your CAD / F3D files for this?  I'm trying to make a gridfinity bin for it, but no matter what i do in F3D, importing the STL files doesn't work great, and i can't seem to make it work.

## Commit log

2022-12-11 Create winder assembled.png
2023-06-26 Add files via upload
    Fixed print orientation
    [GT2 Calibration Wire Pivot 0.032.stl]
2023-07-09 Update Readme.md
    Added BOM spring details
2023-07-09 Update manual to include tension values
2023-08-14 Update Readme.md
    Added alternative calibration image for clarity
2023-08-15 Add files via upload
    Rev. D added voron tension values and alt calibration image
2023-09-14 Update Readme.md
    Updated steps 5 and 6 under "calibration" for clarity
2023-09-14 Add files via upload
    Rev to E. Updated calibration steps for clarity. Replaces preload12 image to include preload screw callout
2023-09-25 Update Readme.md
    Added "piano wire" descriptor to BOM
2023-12-06 Update Readme.md
    Added ASA to recommended materials
2024-01-15 Update Readme.md
    Added recommendation for exit pieces to be used at motor exits
2024-02-22 Add files via upload
    Rev manual to F. Corrected calibration wire metric from 90mm to 100mm. add creality, prusa and bambu tension guidelines
2024-04-23 Create delme.txt
    Added 1515 extrusion versions
2024-12-09 Update Readme.md
    Updated tension tables to include more printers and GT3 (tested identical to GT2)
2024-12-09 Add files via upload
    Rev to C. added tested printer models, included GT3 and additional table parameters
2025-07-02 Create CAD
2025-07-14 Update Readme.md
    Updated music wire source
2025-12-23 Add files via upload
    Blanks added for custom cases, gridfinity, etc.
    [Tension Meter Blank 0.0mm Offset.step, Tension Meter Blank 0.5mm Offset.step, Tension Meter Blank 1.0mm Offset.step]

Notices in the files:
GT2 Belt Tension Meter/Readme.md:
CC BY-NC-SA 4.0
